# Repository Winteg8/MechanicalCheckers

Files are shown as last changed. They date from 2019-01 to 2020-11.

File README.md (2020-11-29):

Video Demo: https://youtu.be/7KSG-KsRqcc 
The project is incomplete, so the arm is missing the electrical magnet to pick up and set down metal checkers. The project is built using ESP-32 Thing, three SG90 servos, a 6V battery pack (four AA batteries), 3D-printed parts for the arm, and some wooden parts for the board and arm support.

Challenges and Design:
The biggest constraints were the 1.80 kg-cm torque and the 180 degrees of freedom of the provided SG90 servos. To accommodate that, I made the following design choices:
1. The base of the arm is located above the center of the board. This way the arm needs to be just long enough to reach the furthest squares at full extension at 45 degrees to all axes.
2. The "elbow" of the arm is operated by a servo that serves as a counter-balance to the rest of the arm, so the "shoulder" joint does not need as much torque.
3. The radial joint is geared 2:1, so 180 degrees of servo rotation is equivalent to 360 degrees of arm rotation. The "shoulder" and "elbow" joints of the arm needed maximum torque without sacrificing the required degree of freedom. The "shoulder" joint servo was geared 1:2 and "elbow" joint servo - 2:3.

Software:
The program takes a list of square positions as input, such as [A1, G5], and performs a motion of taking a piece from A1 to G5. The list of positions can be of arbitrary length, since checkers can jump multiple pieces at once.

Potential improvements:
The movement could be smoothed out using a smoother path of motion for the moved piece and constant acceleration. The code could be implemented more elegantly using ternary operations.

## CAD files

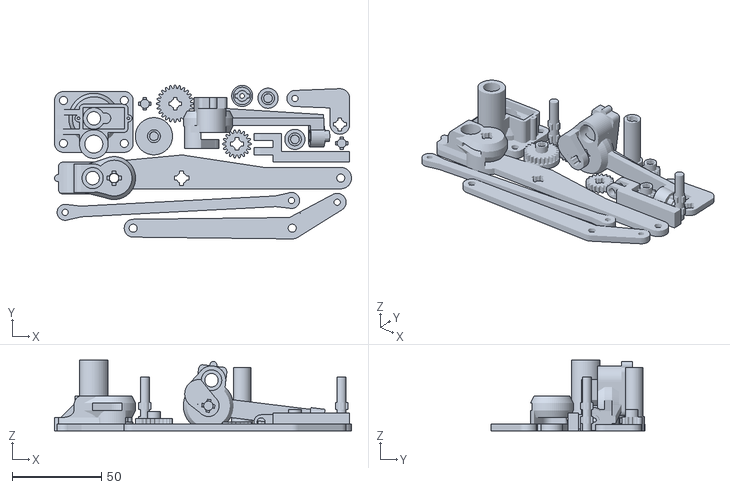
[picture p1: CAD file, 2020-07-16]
Robotic Arm (Print).stl
166.0 x 86.0 x 39.5

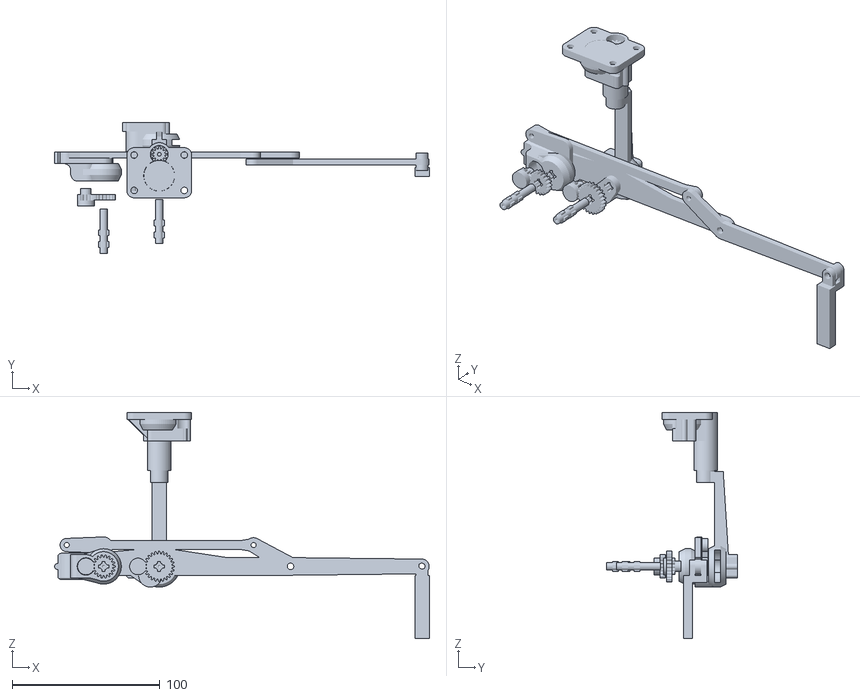
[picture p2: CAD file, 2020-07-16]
Robotic Arm.stl
254.2 x 88.5 x 153.5

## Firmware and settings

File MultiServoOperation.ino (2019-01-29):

//
//  main.c
//  ArmTesting
//
//  Created by Maxim Anaya on 4/9/17.
//  Copyright © 2017 Maxim Anaya. All rights reserved.
//

#include <stdio.h>
#include "esp32-hal-ledc.h"
#include "Arduino.h"
#include "math.h"

// mode
const int pMode = 1;  // 0 for callibrating, 1 for running

// math
const double pie = 3.141592653589793;

// servo capabilities
const int period = 16;
const int minDelay0 = 2575;
const int maxDelay0 = 8425;
const int minDelay1 = 1600;
const int maxDelay1 = 7500;
const int minDelay2 = 1450;
const int maxDelay2 = 7550;
const int minDegree = 0;
const int maxDegree = 180;


// pin configuration
const int switchPin = 13;
const int EMPin = 22;
const int servoPin1 = 19;
const int servoPin2 = 2;
const int servoPin3 = 4;

// mechanical arm specifications (in cm and degrees)
const double B = 20.3200;
const double vClearance = 3; // height above the pickup/dropoff height of electromagnet





// mechanical arm functions
double armLength(double h)
{
    return (hypot(h, h))/2;
}
double height(double b) // B = board length
{
    double len = b*7/16;
    return hypot(len, len);
}
double horizontalDistance(double b, int squaresX, int squaresZ)
{
    float dx = (abs(squaresX) * b / 8) - (b / 16);
    float dz = (abs(squaresZ) * b / 8) - (b / 16);
    
    return (hypot(dx, dz));
}

double servoAngle0(int dx, int dz)
{
    float angle = atan((fabsf((float)dz) - 0.5)/(fabsf((float)dx) - 0.5)) * 180 / pie;

    /*Serial.print("dx = ");
    Serial.println(dx);
    Serial.print("dz = ");
    Serial.println(dz);
    Serial.print("dz/dx = ");
    Serial.println(dz/dx);
    Serial.println(fabsf((float)dz/(float)dx));
    Serial.print("Inter-quadrant angle = ");
    Serial.println(angle);*/
    if (dx > 0)
    {
      if (dz < 0)
        angle = 360 - angle;      // if not 4th quadrant (when x is positive), then 1st quadrant
    }   
    else if (dz > 0)
        angle = 180 - angle;      // 2nd quadrant
    else
        angle += 180;             // 3rd quadrant
    
    return map(angle, 0, 360, 180, 0); // such mapping is due to 2:1 inverse gearbox on the radial servo
}

double deg(double v)
{
    return (v * 180 / pie);
}

double m(double l, double h, double d)
{
    double answer = hypot(h,d)/2/l;
    if (answer > 1)
        return 1;
    else
        return answer;
}

double theta(double m)
{
    return 2*asin(m);
}

double zhe(double m)
{
    return acos(m);
}

double exx(double h, double d)
{
    return atan(h/d);
}

double phi(double l, double h, double d)
{
    return exx(h, d) - zhe(m(l, h, d));
}

double servoAngle1(double l, double h, double d)
{
    //printf("Rad1 = %f \n", phi(l, h, d));
    return deg(phi(l, h, d)) * 2; //map(deg(phi(l, h, d)), 0, 90, 0, 180); // mapping due to servo orientation (flipped 0 and 180)
}

double servoAngle2(double l, double h, double d)
{
    //printf("Rad2 = %f \n", theta(m(l, h, d)));
    return map((deg(theta(m(l, h, d))) - 60), 0, 120, 180, 0); // mapping due to 1.5 inverse gearbox on the servo
}


double doubleCheck(double l, double h, double d)
// returns horizontal distance (center to square) covered by the mechanical arm
{
    double d1 = l * cos(phi(l, h, d));
    double d2 = l * cos(theta(m(l, h, d)) - phi(l, h, d));
    double a2 = deg(theta(m(l, h, d) - phi(l, h, d)));
    
    printf("d1 = %f \n", d1);
    printf("d2 = %f \n", d2);
    printf("a2 = %f \n", a2);
    
    if (a2 >= 120)
    {
        printf("total distance = %f \n", d1+d2);
        return d1+d2;
    }
    else
    {
        printf("total distance = %f \n", d1-d2);
        return d1-d2;
    }
}



void moveComplex(float b, float l, float minD, float minR, float h, int ax, int az, int bx, int bz)
{
    // PROCEDURE:
    // calculate:
    // 1. How many points to calculate on the path from initial to final position
    //      - calculate minimum points to traverse distance (given a maximum distance between 2 points)
    //      - calculate minimum points to traverse angle (given a maximum angle between two angle values)
    //      - number of points for both angle and distance = greater of two minimums
    // 2. Where those poits are located
    // 3. Servo angles for each point
    // 4. Signal lengths mapped from servo angles
    // Output those signal lengths successively in a while loop

    Serial.print("B = ");
    Serial.print(b);
    Serial.print("      L = ");
    Serial.print(l);
    Serial.print("      h = ");
    Serial.print(h);

    
    float d1 = horizontalDistance(b, ax, az);
    float d2 = horizontalDistance(b, bx, bz);
    float a1 = servoAngle0(ax, az);
    float a2 = servoAngle0(bx, bz);
    Serial.print("d1 = ");
    Serial.println(d1);
    Serial.print("Servo1 at d1 = ");
    Serial.println(servoAngle1(l, h, d1));
    Serial.print("Servo2 at d1 = ");
    Serial.println(servoAngle2(l, h, d1));
    
    Serial.print("d2 = ");
    Serial.println(d2);
    Serial.print("Servo1 at d2 = ");
    Serial.println(servoAngle1(l, h, d2));
    Serial.print("Servo2 at d2 = ");
    Serial.println(servoAngle2(l, h, d2));
    
    Serial.print("servo0 1 = ");
    Serial.println(a1);
    Serial.print("servo0 2 = ");
    Serial.println(a2);
    
    // 1
    float minLinearPts = ceil(fabsf((d2 - d1)/minD));
    float minRadialPts = ceil(fabsf((a2 - a1)/minR));

    Serial.print("minLinearPts = fabsf(");
    Serial.print(d2);
    Serial.print(" - ");
    Serial.print(d1);
    Serial.print(") / ");
    Serial.print(minD);
    Serial.print(" = ");
    Serial.print(fabsf(d2-d1));
    Serial.print(" / ");
    Serial.print(minD);
    Serial.print(" = ");
    Serial.print((fabsf(d2-d1)) / minD);
    Serial.print(" == ");
    Serial.println(minLinearPts);
    Serial.print("minRadialPts = ");
    Serial.println(minRadialPts);
    
    if (minLinearPts > minRadialPts)
        minRadialPts = minLinearPts;
    else
        minLinearPts = minRadialPts;
        
    float intervalDist = (d2 - d1)/minLinearPts;
    float intervalAngl = (a2 - a1)/minRadialPts;

    Serial.println("Both are set to:");
    Serial.print("linear = ");
    Serial.println(minLinearPts);
    Serial.print("radial = ");
    Serial.println(minRadialPts);
    
    Serial.print("linearInterval = ");
    Serial.println(intervalDist);
    Serial.print("radialInterval = ");
    Serial.println(intervalAngl);
    
    // 2
    float linPts[(int)minLinearPts + 1];
    float radPts[(int)minRadialPts + 1];
    
    for (int i = 0; i <= (int)minLinearPts; i++)
    {
      linPts[i] = d1 + i * intervalDist;
      radPts[i] = a1 + i * intervalAngl;
    }
    
    // 3
    //float servo0[(int)minLinearPts];
    float servo1[(int)minLinearPts];
    float servo2[(int)minLinearPts];
    
    for (int i = 0; i <= (int)minLinearPts; i++)
    {
        // no need to convert angle to angle, only distance to angle
        servo1[i] = servoAngle1(l, h, linPts[i]);
        servo2[i] = servoAngle2(l, h, linPts[i]);

    }

    float value;
    Serial.println("MOVING...");
    Serial.println("---------------------");
    // 4
    for (int i = 0; i <= (int)minLinearPts; i++)
    {
        ledcWrite(1, map(radPts[i], minDegree, maxDegree, minDelay0, maxDelay0));
        ledcWrite(2, map(servo1[i], minDegree, maxDegree, minDelay1, maxDelay1));
        ledcWrite(3, map(servo2[i], minDegree, maxDegree, minDelay2, maxDelay2));
        Serial.print("servo0 = ");
        Serial.print(radPts[i]);
        Serial.print("              servo1 = ");
        Serial.print(servo1[i]);
        Serial.print("              servo2 = ");
        Serial.println(servo2[i]);

        delay(10);
    }
}
/*
void moveLinear(float B, float L, float minD, float h, int ax, int az, int bx, int bz)
{
    // PROCEDURE:
    // calculate:
    // 1. How many points to calculate on the path from initial to final position
    //      - calculate minimum points to traverse distance (given a maximum distance between 2 points)
    // 2. Where those poits are located
    // 3. Servo angles for each point
    // 4. Signal lengths mapped from servo angles
    // Output those signal lengths successively in a while loop
    // ----------------------------------------
    
    float d1 = horizontalDistance(B, ax, az);
    float d2 = horizontalDistance(B, bx, bz);
    
    // 1
    float minLinearPts = ceil(fabsf((d2 - d1)/minD));
    float intervalDist = (d2 - d1)/minLinearPts;
    
    // 2
    float points[(int)minLinearPts];
    if (d2 > d1)
        for (int i = 0; i < (int)minLinearPts; i++)
            points[i] = d1 + i * intervalDist;
    else
        for (int i = 0; i < (int)minLinearPts; i++)
            points[i] = d1 - i * intervalDist;
    
    // 3
    //float servo0[(int)minLinearPts];
    float servo1[(int)minLinearPts];
    float servo2[(int)minLinearPts];
    
    for (int i = 0; i < (int)minLinearPts; i++)
    {
        servo1[i] = servoAngle1(L, h, points[i]);
        servo2[i] = servoAngle2(L, h, points[i]);
    }
    
    // 4
    for (int i = 0; i < (int)minLinearPts; i++)
    {
        servo1[i] = map(servo1[i], 0, 180, 1000, 2000);
        servo2[i] = map(servo2[i], 0, 180, 1000, 2000);
    }
    
    for (int i = 0; i < (int)minLinearPts; i++)
    {
        ledcWrite(1, servo1[i]);
        ledcWrite(2, servo2[i]);
        
        delay(10);
    }
}*/

void moveVertically(float b, float l, float minD, float h1, float h2, int x, int z)
{
    float d = horizontalDistance(b, x, z);

    Serial.println("VERTICAL MOVE");
    Serial.print("d = ");
    Serial.println(d);
    Serial.print("h1 = ");
    Serial.println(h1);
    Serial.print("Servo1 at h1 = ");
    Serial.println(servoAngle1(l, h1, d));
    Serial.print("Servo2 at h1 = ");
    Serial.println(servoAngle2(l, h1, d));
    
    Serial.print("h2 = ");
    Serial.println(h2);
    Serial.print("Servo1 at h2 = ");
    Serial.println(servoAngle1(l, h2, d));
    Serial.print("Servo2 at h2 = ");
    Serial.println(servoAngle2(l, h2, d));
    Serial.println();
    
    // 1
    float minLinearPts = ceil(fabsf((h2 - h1)/minD));
    float intervalDist = (h2 - h1)/minLinearPts;
    
    // 2
    float points[(int)minLinearPts + 1];
      for (int i = 0; i <= (int)minLinearPts; i++)
            points[i] = h1 + i * intervalDist;
        
    // 3
    //float servo0[(int)minLinearPts];
    float servo1[(int)minLinearPts];
    float servo2[(int)minLinearPts];
    
    for (int i = 0; i <= (int)minLinearPts; i++)
    {
        servo1[i] = servoAngle1(l, points[i], d);
        servo2[i] = servoAngle2(l, points[i], d);
        /*Serial.print(i);
        Serial.print(". heght = ");
        Serial.print(points[i]);
        Serial.print("     a1 = ");
        Serial.print(servo1[i]);
        Serial.print("     a2 = ");
        Serial.println(servo2[i]);*/
        
    }
    
    // 4
    for (int i = 0; i <= (int)minLinearPts; i++)
    {
        ledcWrite(2, map(servo1[i], minDegree, maxDegree, minDelay1, maxDelay1));
        ledcWrite(3, map(servo2[i], minDegree, maxDegree, minDelay2, maxDelay2));
        Serial.print("servo1 = ");
        Serial.print(servo1[i]);
        Serial.print("              servo2 = ");
        Serial.println(servo2[i]);
        
        delay(20);
    }
}

void pickUp(float b, float l, float minD, float minR, float hHigh, float hLow, int ax, int az, int bx, int bz)
{
    // pre conditions: arm is at [ax, az] coords at hCarry height.
    // PROCEDURE:
    // 1. move linearly and/or radially
    // 2. call moveInterval to move vertically to height hReg
    // 3. toggle the electromagnet
    // 4. call moveInterval to move vertically to height hCarry
    
    
    moveComplex(b, l, minD, minR, hHigh, ax, az, bx, bz);
    delay(300);
    moveVertically(b, l, minD, hHigh, hLow, bx, bz);
    delay(150);
    pinMode(EMPin, HIGH); // turn electromagnet ON
    delay(150);
    moveVertically(b, l, minD, hLow, hHigh, bx, bz);
    delay(300);
}

void dropOff(float b, float l, float minD, float minR, float hHigh, float hLow, int ax, int az, int bx, int bz)
{
    // pre conditions: arm is at [ax, az] coords at hCarry height.
    // PROCEDURE:
    // 1. move linearly and/or radially
    // 2. call moveInterval to move vertically to height hReg
    // 3. toggle the electromagnet
    // 4. call moveInterval to move vertically to height hCarry
    
    
    moveComplex(b, l, minD, minR, hHigh, ax, az, bx, bz);
    delay(300);
    moveVertically(b, l, minD, hHigh, hLow, bx, bz);
    delay(150);
    pinMode(EMPin, LOW); // turn electromagnet OFF
    delay(150);
    moveVertically(b, l, minD, hLow, hHigh, bx, bz);
    delay(300);
}

void removePiece(float b, float l, float minD, float minR, float h, int dx, int dz)
{
    // same as moveComplex, but the destination is always off the board (where the eaten pieces are)
  // PROCEDURE:
    // calculate:
    // 1. How many points to calculate on the path from initial to final position
    //      - calculate minimum points to traverse distance (given a maximum distance between 2 points)
    //      - calculate minimum points to traverse angle (given a maximum angle between two angle values)
    //      - number of points for both angle and distance = greater of two minimums
    // 2. Where those poits are located
    // 3. Servo angles for each point
    // 4. Signal lengths mapped from servo angles
    // Output those signal lengths successively in a while loop
    
    float d1 = horizontalDistance(b, dx, dz);
    float d2 = 12.5;
    float a1 = servoAngle0(dx, dz);
    float a2 = 45;
    Serial.print("d1 = ");
    Serial.println(d1);
    Serial.print("Servo1 at d1 = ");
    Serial.println(servoAngle1(l, h, d1));
    Serial.print("Servo2 at d1 = ");
    Serial.println(servoAngle2(l, h, d1));
    
    Serial.print("d2 = ");
    Serial.println(d2);
    Serial.print("Servo1 at d2 = ");
    Serial.println(servoAngle1(l, h, d2));
    Serial.print("Servo2 at d2 = ");
    Serial.println(servoAngle2(l, h, d2));
    
    Serial.print("servo0 1 = ");
    Serial.println(a1);
    Serial.print("servo0 2 = ");
    Serial.println(a2);
    
    // 1
    float minLinearPts = ceil(fabsf((d2 - d1)/minD));
    float minRadialPts = ceil(fabsf((a2 - a1)/minR));

    Serial.print("minLinearPts = fabsf(");
    Serial.print(d2);
    Serial.print(" - ");
    Serial.print(d1);
    Serial.print(") / ");
    Serial.print(minD);
    Serial.print(" = ");
    Serial.print(fabsf(d2-d1));
    Serial.print(" / ");
    Serial.print(minD);
    Serial.print(" = ");
    Serial.print((fabsf(d2-d1)) / minD);
    Serial.print(" == ");
    Serial.println(minLinearPts);
    Serial.print("minRadialPts = ");
    Serial.println(minRadialPts);
    
    if (minLinearPts > minRadialPts)
        minRadialPts = minLinearPts;
    else
        minLinearPts = minRadialPts;
        
    float intervalDist = (d2 - d1)/minLinearPts;
    float intervalAngl = (a2 - a1)/minRadialPts;

    Serial.println("Both are set to:");
    Serial.print("linear = ");
    Serial.println(minLinearPts);
    Serial.print("radial = ");
    Serial.println(minRadialPts);
    
    Serial.print("linearInterval = ");
    Serial.println(intervalDist);
    Serial.print("radialInterval = ");
    Serial.println(intervalAngl);
    
    // 2
    float linPts[(int)minLinearPts + 1];
    float radPts[(int)minRadialPts + 1];
    
    for (int i = 0; i <= (int)minLinearPts; i++)
    {
      linPts[i] = d1 + i * intervalDist;
      radPts[i] = a1 + i * intervalAngl;
    }
    
    // 3
    //float servo0[(int)minLinearPts];
    float servo1[(int)minLinearPts];
    float servo2[(int)minLinearPts];
    
    for (int i = 0; i <= (int)minLinearPts; i++)
    {
        // no need to convert angle to angle, only distance to angle
        servo1[i] = servoAngle1(l, h, linPts[i]);
        servo2[i] = servoAngle2(l, h, linPts[i]);
        /*Serial.print(i);
        Serial.print(". distance = ");
        Serial.print(linPts[i]);
        Serial.print("     a1 = ");
        Serial.print(servo1[i]);
        Serial.print("     a2 = ");
        Serial.println(servo2[i]);*/
    }

    float value;
    Serial.println("MOVING...");
    Serial.println("---------------------");
    // 4
    for (int i = 0; i <= (int)minLinearPts; i++)
    {
        ledcWrite(1, map(radPts[i], minDegree, maxDegree, minDelay0, maxDelay0));
        ledcWrite(2, map(servo1[i], minDegree, maxDegree, minDelay1, maxDelay1));
        ledcWrite(3, map(servo2[i], minDegree, maxDegree, minDelay2, maxDelay2));
        delay(10);
    }

    pinMode(EMPin, LOW); // turn off electromagnet
}

int checkerX(char x)
{
  switch (x)
  {
    case 'a':
      return -4;
    case 'b':
      return -3;
    case 'c':
      return -2;
    case 'd':
      return -1;
    case 'e':
      return 1;
    case 'f':
      return 2;
    case 'g':
      return 3;
    case 'h':
      return 4;
  }
}

int checkerZ(int z)
{
  if (z > 4)
    return (z - 4);
  else
    return (z - 5);
}


void turn(float a1, float a2, float maxR, int p, int servoNum)
{
  // function meant for servo callibration
  
  int numPts = ceil(fabsf(a2 - a1) / maxR);
  Serial.print("numPts = ");
  Serial.println(numPts);
  float angleInterval = (a2 - a1) / numPts;
  Serial.print("Interval angle = ");
  Serial.println(angleInterval);
  Serial.print("Distance to cover = ");
  Serial.println(numPts*angleInterval);
  Serial.print("Starting at ");
  Serial.println(a1);
  //Serial.print(", ending at 
  float value = 0;
  float minD = 0;
  float maxD = 0;

  switch (servoNum)
  {
    case 0:
    {
      minD = minDelay0;
      maxD = maxDelay0;
    }
    case 1:
    {
      minD = minDelay1;
      maxD = maxDelay1;
    }
    case 2:
    {
      minD = minDelay2;
      maxD = maxDelay2;
    }
  }

  
  for (int i = 0; i <= numPts; i++)
  {
    value = a1 + i * angleInterval;
    Serial.print("valPos = ");
    Serial.println(value);
    ledcWrite((servoNum + 1), map(value, minDegree, maxDegree, minD, maxD));
    delay(p);
  }

  delay(1000);
}






void setup()
{
    Serial.begin(9600);
    // mechanical arm calculations
    const double hReg = height(B);
    const double hCarry = hReg - vClearance;
    const double L = armLength(hReg);
    int dx = 4;
    int dz = 4;
    
    double d = horizontalDistance(B, dx, dz);
    double dmax = horizontalDistance(B, 4, 4);
    
    int servo1_1 = 0;
    int servo1_2 = servoAngle1(L, hReg, d);
    int servo2_1 = 0;
    int servo2_2 = servoAngle2(L, hReg, d);
    
    
    printf("\nBoard length = ");
    printf("%f \n", B);
    printf("Maximum distance d = ");
    printf("%f \n", dmax);
    printf("L = ");
    printf("%f \n", L);
    printf("Custom distance = ");
    printf("%f \n", d);
    printf("\n   Piece pickup/drop values: \n");
    printf("h = ");
    printf("%f \n", hReg);
    //printf("Hypotenuse = ");
    //printf("%f \n", hyp);
    
    
    servo1_2 = servoAngle1(L, hReg, d);
    printf("Servo 1 angle = ");
    printf("%d \n", servo1_2);
    servo2_2 = servoAngle2(L, hReg, d);
    printf("Servo 2 angle = ");
    printf("%d \n", servo2_2);
    doubleCheck(L, hReg, d);
    
    printf("\n   Piece carrying values: \n");
    printf("h = ");
    printf("%f \n", hCarry);
    servo1_1 = servoAngle1(L, hCarry, d);
    printf("Servo 1 angle = ");
    printf("%d \n", servo1_1);
    servo2_1 = servoAngle2(L, hCarry, d);
    printf("Servo 2 angle = ");
    printf("%d \n", servo2_1);
    doubleCheck(L, hCarry, d);


    pinMode(switchPin, INPUT);
    pinMode(EMPin, OUTPUT);
    ledcSetup(1, 50, period); // channel 1, 50 Hz, 16-bit width
    ledcAttachPin(servoPin1, 1);   // GPIO 19 assigned to channel 1
    ledcSetup(2, 50, 16); // channel 2, 50 Hz, 16-bit width
    ledcAttachPin(servoPin2, 2);   // GPIO 2 assigned to channel 2
    ledcSetup(3, 50, period); // channel 3, 50 Hz, 16-bit width
    ledcAttachPin(servoPin3, 3);   // GPIO 4 assigned to channel 3

    Serial.println();
    Serial.println("Radial angle check");
    Serial.println("-------------------------");
    char letter = 'a';
    int number = 1;
    Serial.println(servoAngle0(checkerX(letter), checkerZ(number)));
    
}

void loop()
{
  if (digitalRead(switchPin) == 1)
  {
    const double hReg = height(B);
    const double hCarry = hReg - vClearance;
    const double L = armLength(hReg);
    const float minLinear = 0.25; // [cm]
    const float minRadial = 2; // [degrees]

   

    if (digitalRead(switchPin) == 1)
    {
      if (pMode == 1)
      {
        pickUp(B, L, minLinear, minRadial, hCarry, hReg, -4, -4, 1, 1);
        //dropOff(B, L, minLinear, minRadial, hCarry, hReg, 1, 1, -4, -4);
        dropOff(B, L, minLinear, minRadial, hCarry, hReg, 1, 1, -3, 4);
        pickUp(B, L, minLinear, minRadial, hCarry, hReg, -3, 4, -2, 1);
        dropOff(B, L, minLinear, minRadial, hCarry, hReg, -2, 1, -4, -4);
      }
      else if (pMode == 0)
      {
        turn(0, 180, 1, 20, 0);
        if (digitalRead(switchPin) == 1)
          turn(180, 0, 1, 20, 0);
      }
    }  
  }
}

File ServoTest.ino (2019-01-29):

#include "Arduino.h"

const int minDelay = 500;
const int maxDelay = 2300;
const int minDegree = 0;
const int maxDegree = 180;
const int switchPin = 13;
const int servoPin = 2;


const int degree1 = 0;
const int degree2 = 180;
int delay1 = 0;
int delay2 = 0;
void setup() 
{
  pinMode(servoPin, OUTPUT);
  pinMode(switchPin, INPUT);
  Serial.begin(9600);
}

void loop()
{
  delay1 = map(degree1, minDegree, maxDegree, minDelay, maxDelay);
  delay2 = map(degree2, minDegree, maxDegree, minDelay, maxDelay);
  Serial.println(delay1);
  Serial.println(delay2);

  // find the mean of the two delays
  float mean = (delay1 + delay2) / 2;
  float acceleration = 0.1;
  float jerk = 0.02;
  Serial.print ("acceleration = ");
  Serial.println(acceleration);
  float sum = 0;
  
  int switchVal = digitalRead(switchPin);
  Serial.println("Moving up...");
  for (float i = delay1; i < delay2; i+=sum)
  {
    if (i <= mean)
    {
      sum += acceleration;
      acceleration += jerk; 
    }
    
    if (switchVal == 1)
    {
      digitalWrite(servoPin, HIGH);
      delayMicroseconds(i);
      digitalWrite(servoPin, LOW);
    }

    if (i > mean)
    {
      acceleration -= jerk;
      sum -= acceleration;
      
    }

    
    Serial.print(sum);
    Serial.print("   ");
    Serial.println(i);

    delay(3);
  }
  delay(1000);


  switchVal = digitalRead(switchPin);
  Serial.println("Moving down...");
  /*
  for (int i = delay2; i > delay1; i-=2)
  {
    if (switchVal == 1)
    {
      digitalWrite(servoPin, HIGH);
      delayMicroseconds(i);
      digitalWrite(servoPin, LOW);
    }
    
    delay(3);
  }*/
  sum = 0;
  for (float i = delay2; i > delay1; i-=sum)
  {
    if (i >= mean)
    {
      sum += acceleration;
      acceleration += jerk; 
    }

    if (switchVal == 1)
    {
      digitalWrite(servoPin, HIGH);
      delayMicroseconds(i);
      digitalWrite(servoPin, LOW);
    }

    if (i < mean)
    {
      acceleration -= jerk;
      sum -= acceleration;
      
    }
    
    Serial.print(sum);
    Serial.print("   ");
    Serial.println(i);

    delay(3);
  }
  delay(1000);
    

  
  
}

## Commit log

2019-01-29 Robotic Arm Movement Code
    RoboticArm2.0 takes a sequence of checkerboard spaces and moves the
    checker through those squares. For example, when given a sequence [a3,
    b4], the arm will pick up the checker at a3 and move it to b4. These
    files were written to run on ESP32.
2020-07-16 3D models for printing and assembly
    [Robotic Arm (Print).stl, Robotic Arm.stl]
